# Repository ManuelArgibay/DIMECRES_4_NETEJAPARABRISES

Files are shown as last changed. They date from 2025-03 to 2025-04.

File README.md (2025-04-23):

# LIMPIA PARABRISAS

## Autores
- ManuelArgibay
- AlexY0916

## Versión - v1.01 Curso - Asignatura de Diseño de PCBs con KiCad - Curso 2024 - 2025

## Objectivo, Descripción breve del objectivo del proyecto.
Diseñar una placa PCB que desarrolle la función de limpiaparabrisas de un automóvil, mediante la detección de lluvia y accionamiento de motores, bombas de agua y un calefactor. Con el objetivo de mantener el parabrisas limpio y libre de objetos que puedan dificultar la visibilidad y evitar accidentes 

## Requisitos y especificaciones
- 2 motores con finales de carrera
- 2 bombas de líquido limpia parabrisas
- Sensor digital de lluvia
- Calefactor del vidrio

## Diagrama de bloques

## Tabla de componentes
| Descripción | Manufacturer Number | Package | Datasheet | Proveedor | Unidades |
| Microcontrolador | PIC18F258 | SOIC-28 | https://www.mouser.es/ProductDetail/Microchip-Technology/PIC18F258-I-SP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 | Mouser | 1 |
|Transceptor|MCP2551|SOIC-8|https://ww1.microchip.com/downloads/en/devicedoc/20001667g.pdf|Microchip|1|
|Amplificador operacional|LT1716|SOIC-5|https://www.mouser.es/datasheet/2/609/LT1716-1716222.pdf|Mouser|2|
|Regulador de tensión|LM117|TO-220|https://www.ti.com/lit/ds/symlink/lm1117.pdf?ts=1742942595976&ref_url=https%253A%252F%252Fbr.mouser.com%252F|Mouser|1|
|Puente H|DRV8871DDA|DDA|https://www.ti.com/lit/ds/symlink/drv8871-q1.pdf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||2|

## Funcionalidades
- Control de motores de limpiaparabrisas, bomba de agua y calefactor
- Detección de lluvia mediante sensor
- Botonera de acción manual

## Historial de cambios | Fecha | Autor | Branch | Descripción |
|1|25/03/2025|ManuelArgibay|main|Creación del proyecto|
|2|25/03/2025|ManuelArgibay|main|Cambio titulo del proyecto|
|3|25/03/2025|ManuelArgibay|main|Modificación del esquemático y pptx|
|4|25/03/2025|ManuelArgibay|main|Agrego net classes, proyecto y presentación |
|5|25/03/2025|AlexY0916|main|Modifico net classes, fc, GNDPWR, separación botonera|
|6|26/03/2025|AlexY0916|main|Separacion del circuito|
|7|29/03/2025|ManuelArgibay|main|Agrego presentaciones y archivos|
|8|29/03/2025|ManuelArgibay|main|Modifico simulaciones del comparador y arreglo esquematico|
|9|30/03/2025|AlexY0916|main|Ordenar esquematico|
|10|30/03/2025|AlexY0916|main|Footprint|
|11|30/03/2025|AlexY0916|main|Arreglar errores con los esquematicos|
|12|30/03/2025|AlexY0916|main|Empezando a añadir el sensor|
|13|31/03/2025|AlexY0916|main|Sensor|
|14|31/03/2025|AlexY0916|main|ICSP|
|15|31/03/2025|ManuelArgibay|main|Arreglo net classes y agrego DB-9|
|16|31/03/2025|ManuelArgibay|main|Empiezo layout, cambio footprints y arreglo esquematico|
|17|01/04/2025|ManuelArgibay|main|Termino layout|
|18|01/04/2025|ManuelArgibay|main|Arreglo nodos no conectados|
|19|01/04/2025|AlexY0916|main|Cambio el cristal|
|20|01/04/2025|AlexY0916|main|Cambio de presentacion, minimas correcciones en el esquematico|
|21|01/04/2025|AlexY0916|main|Nombrar etiqueta PCB|
|22|01/04/2025|AlexY0916|main|Cambio en la presentacion|
|23|02/04/2025|ManuelArgibay|main|Arreglo errores y cambio conector|
|24|02/04/2025|ManuelArgibay|main|Arreglo errores del DRC. Falta arreglar errores del GNDPWR|
|25|02/04/2025|ManuelArgibay|main|Preentrega final|
|26|02/04/2025|ManuelArgibay|main|Agrego cambios|
|27|07/04/2025|ManuelArgibay|main|Arreglo layout y esquematico con las correcciones pasadas|
|28|07/04/2025|AlexY0916|main|Separacion de la botonera|
|29|07/04/2025|AlexY0916|main|Cambio de valor los condensadores del oscilador|
|30|07/04/2025|AlexY0916|main|Cambio diagrama de bloques|
|31|08/04/2025|AlexY0916|main|Reglas de diseño|
|32|08/04/2025|AlexY0916|main|Cambiar esquematico|
|33|08/04/2025|AlexY0916|main|Cambio de la PCB (cambio de conectores)|
|34|09/04/2025|AlexY0916|main|Layout|
|35|09/04/2025|AlexY0916|main|Cambio del sensor|
|36|23/04/2025|ManuelArgibay|main|Arreglo layout y esquematico (DRC correcto)|

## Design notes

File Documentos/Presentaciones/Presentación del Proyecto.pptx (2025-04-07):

## Proyecto: Limpiaparabrisas

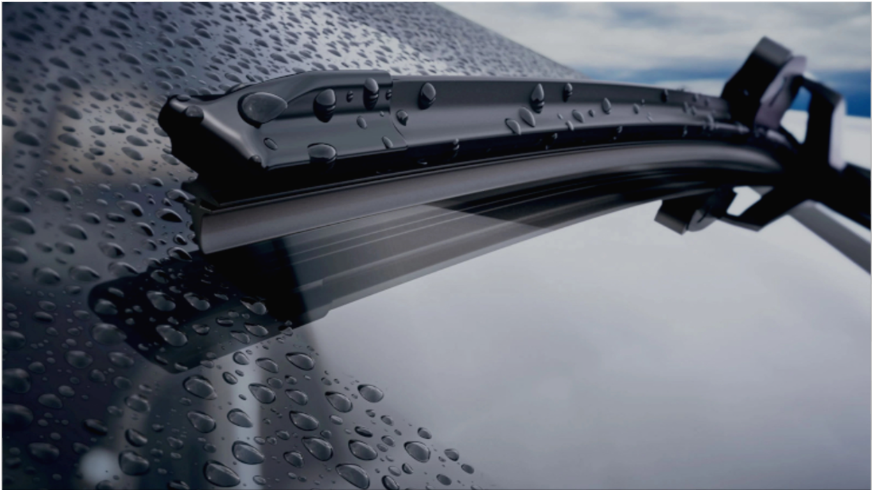
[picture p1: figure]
Les Escombretes Eixugaparabrises - Rodi Motor Services

Argibay Molina Manuel, Yang Alex

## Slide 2

Funcionalidad y objetivos

- Mantener el parabrisas limpio y libre de elementos que obstruyan la visión
  - Escobillas limpiaparabrisas controladas por motores.
  - Bombas de líquido limpia parabrisas.
  - Calefactor que evita el empañamiento del parabrisas.
  - Interfaz manual mediante botonera

- Diseñar e implementar este sistema en una PCB.
  - Garantizar funcionamiento y fiabilidad en el producto.
  - Optimización de energía.
  - Optimización de costos.

## Componentes

Microcontrolador PIC18FXX8
Transceptor MCP2551
Bus de programación y debug
Bus CAN
Bus I^2 C
Botonera

- Fuente de 12V
- Regulador de tensión
- 2 motores DC
- 2 bombas de líquido limpiaparabrisas
- Sensor digital de lluvia
- Calefactor del vidrio
- 2 puentes “H”
- 2 relés electromagnéticos
- 2 finales de carreras magnéticos

## Diagrama de Bloques

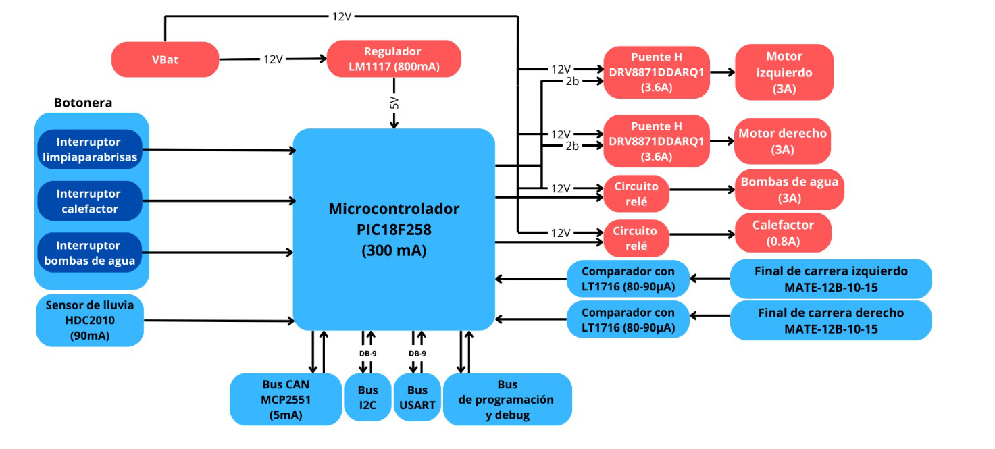
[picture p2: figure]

## Regulador de tensión

LM1117

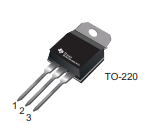
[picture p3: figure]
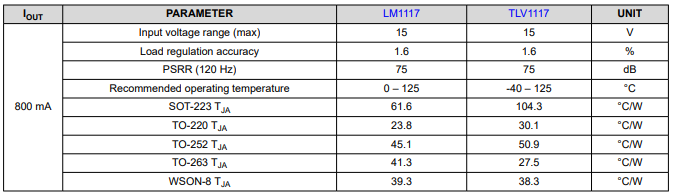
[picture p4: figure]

## Detector de lluvia

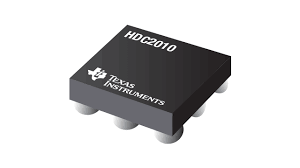
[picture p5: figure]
HDC2010 - Low Power Humidity and Temperature Sensor - Electronics-Lab.com

HDC2010

## Puente H

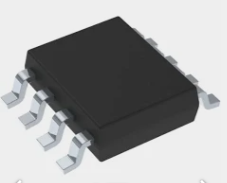
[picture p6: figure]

DRV8871DDARQ1

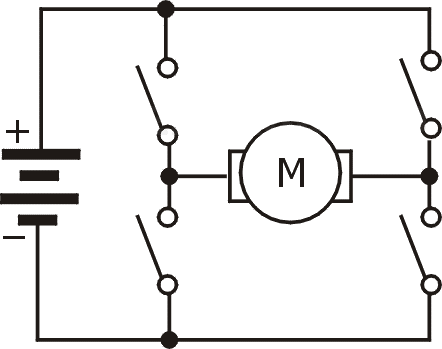
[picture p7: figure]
Control mediante puente en H | Control y robótica 4º E.S.O.

## Final de Carrera magnético (Reed Switch)

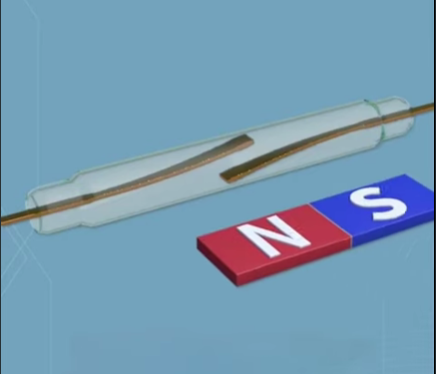
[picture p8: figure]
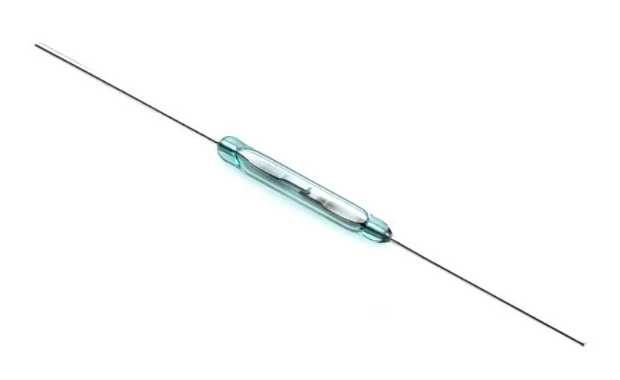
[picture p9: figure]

MATE-12B-10-15

## Amplificador Operacional

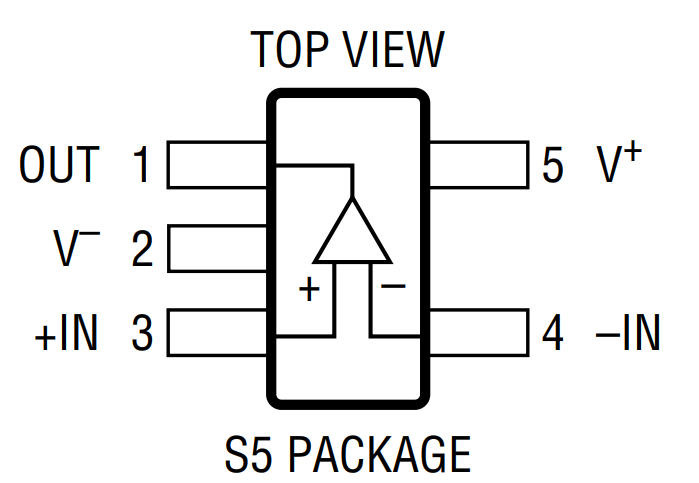
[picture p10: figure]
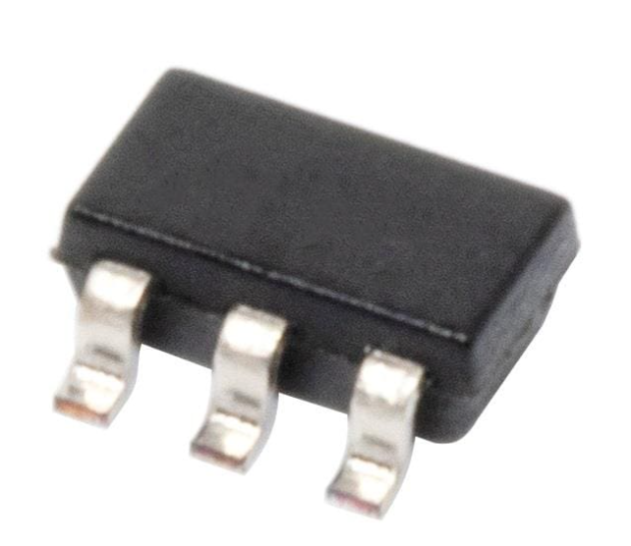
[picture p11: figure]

LT1716

## Esquemático del circuito

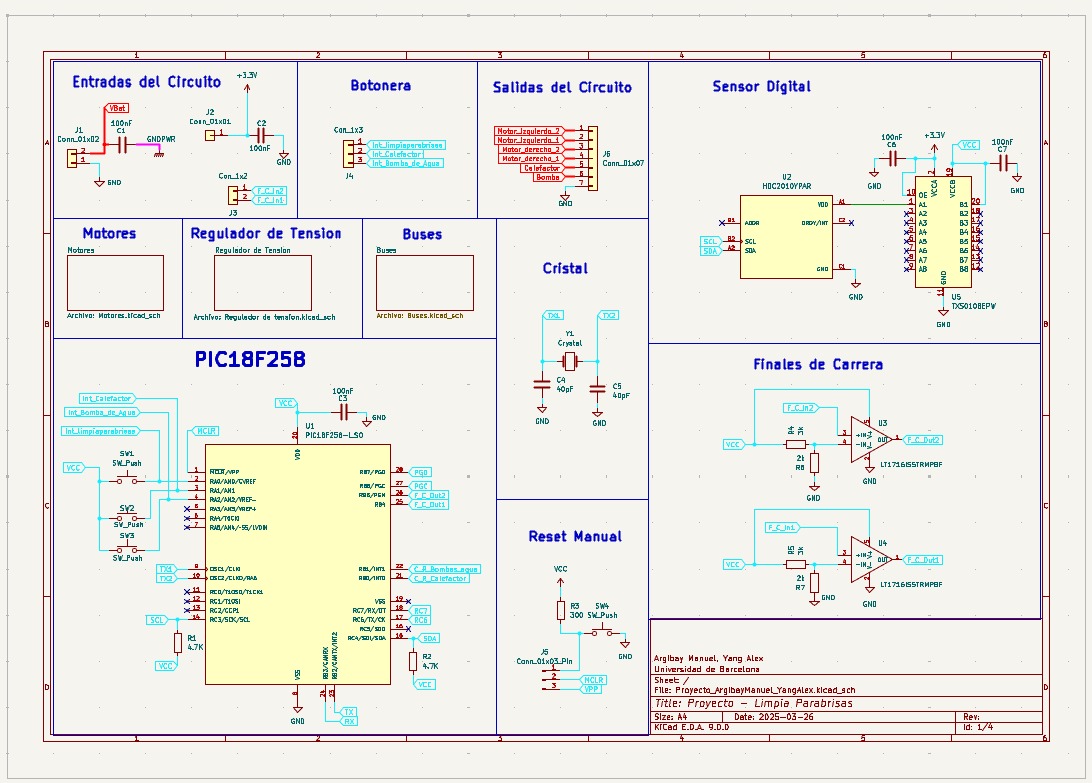
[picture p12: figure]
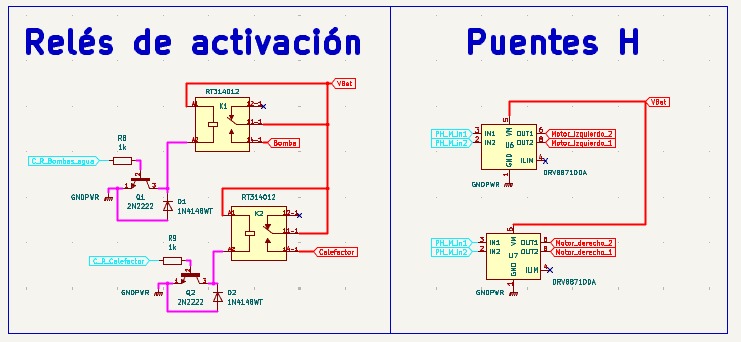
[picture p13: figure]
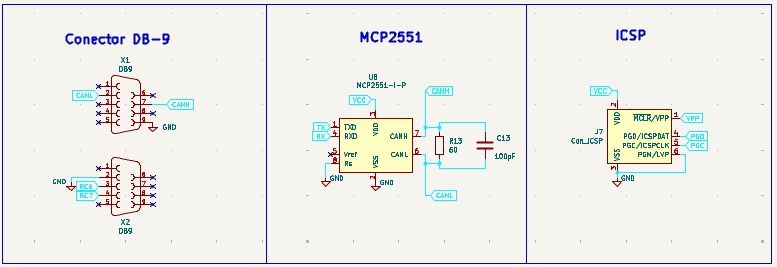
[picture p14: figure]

## Cambios

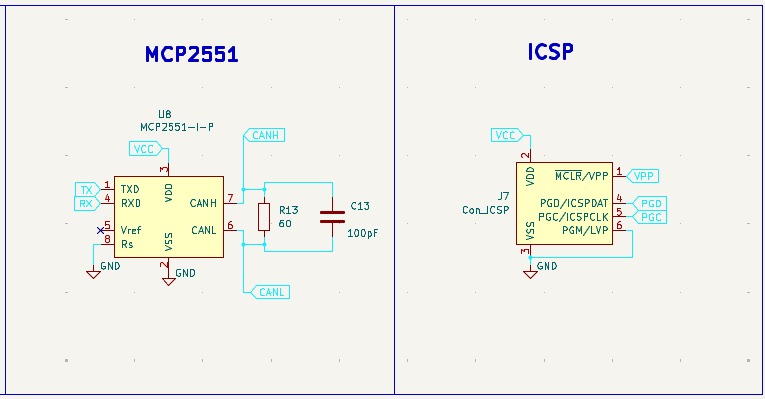
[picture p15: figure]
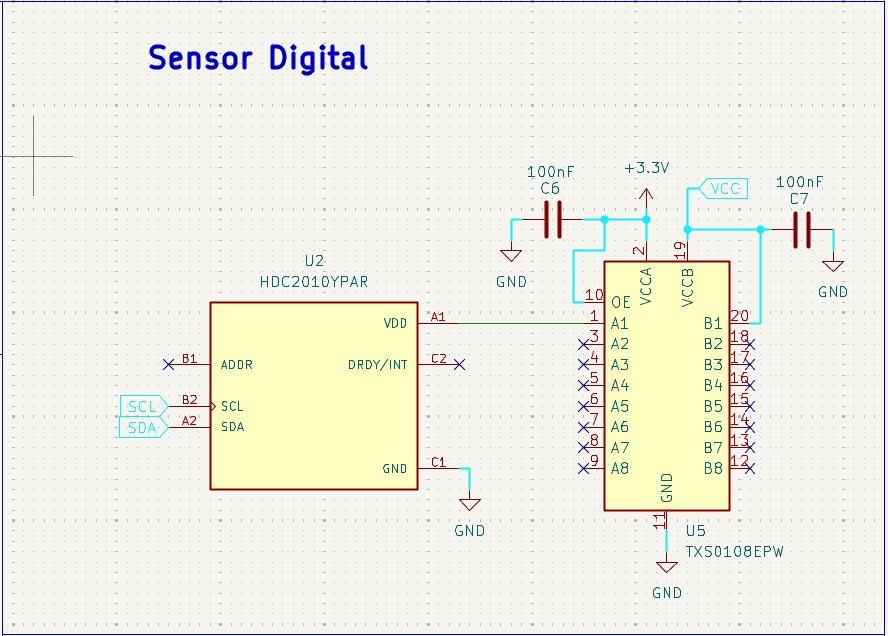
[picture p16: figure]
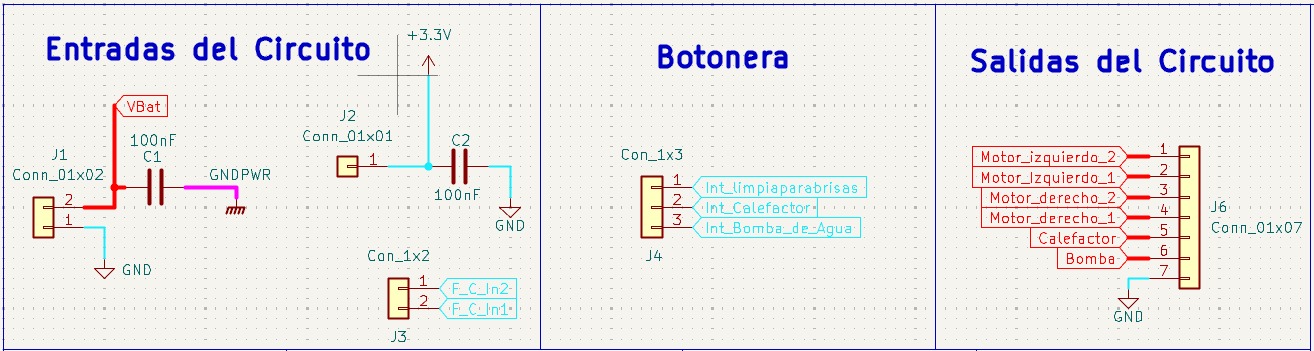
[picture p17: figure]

## Layout (TOP)

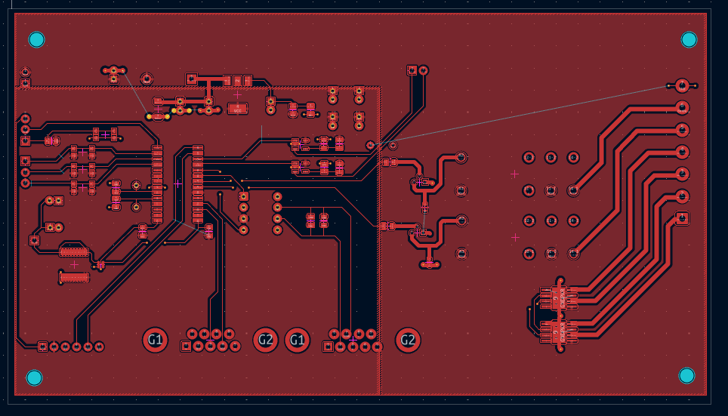
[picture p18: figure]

## Bottom

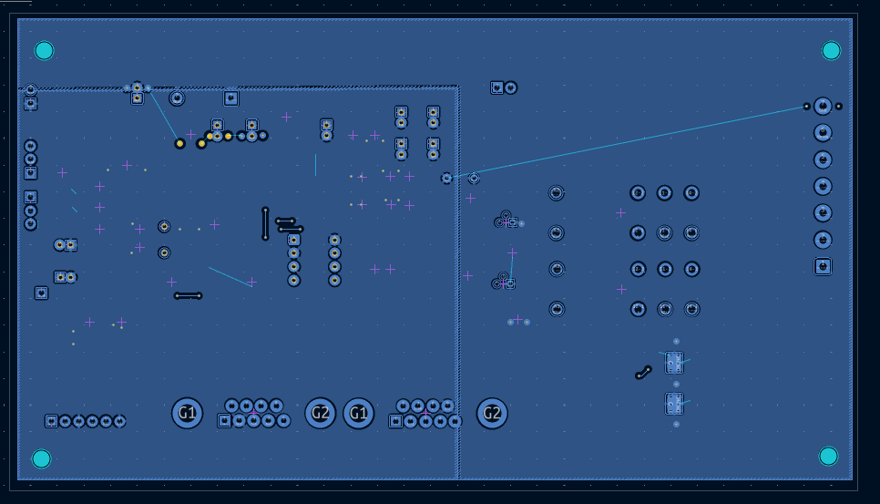
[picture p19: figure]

## Cosas a destacar del Layout

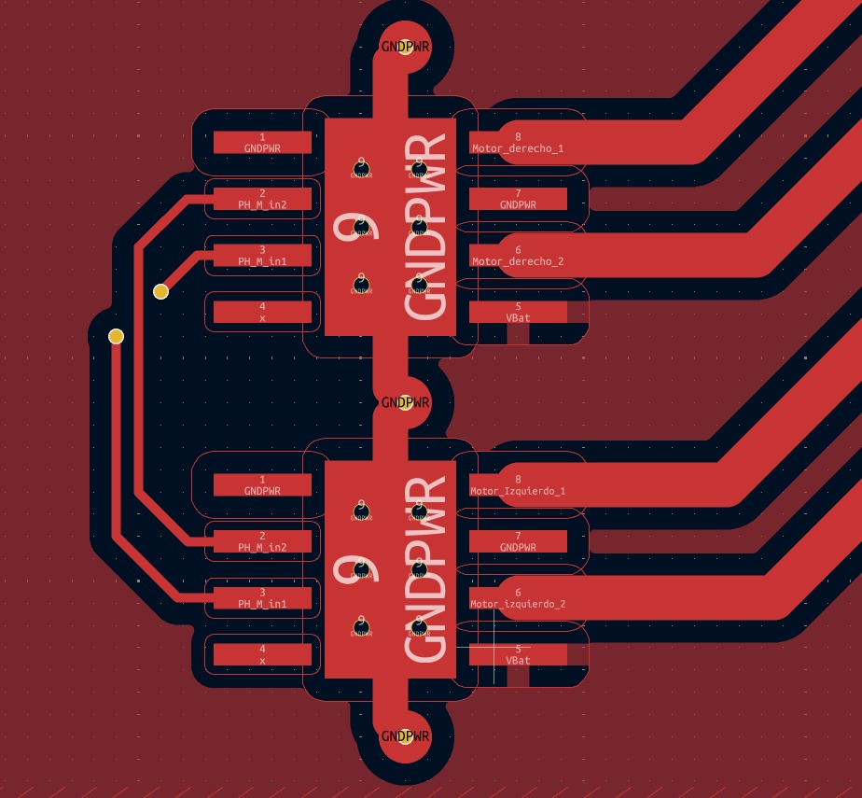
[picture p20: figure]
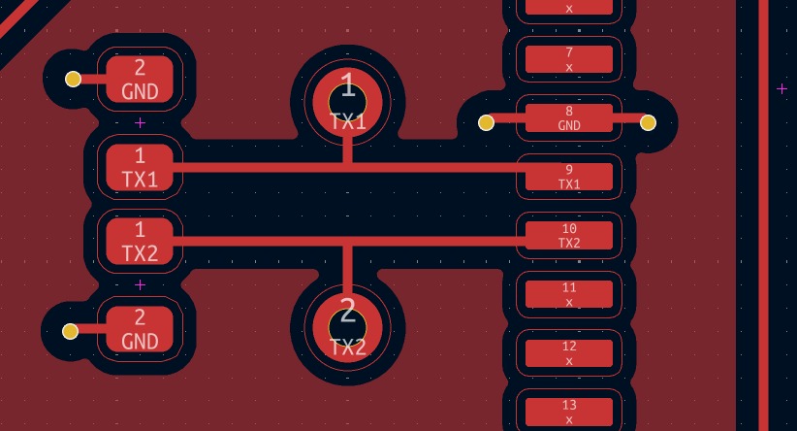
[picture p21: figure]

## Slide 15

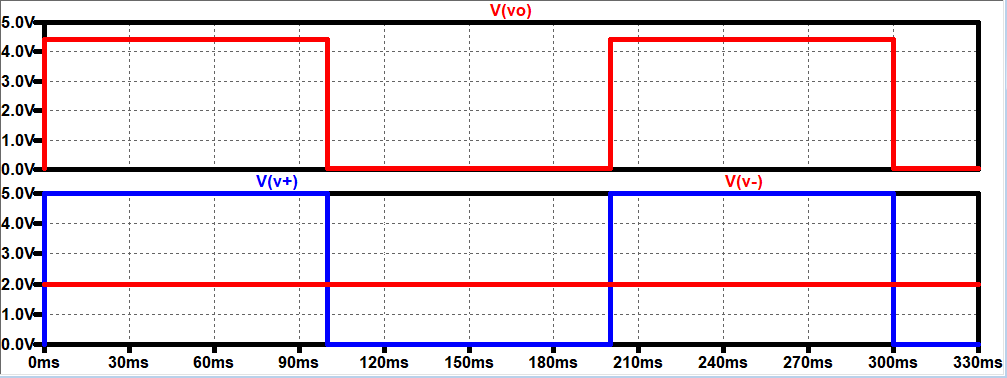
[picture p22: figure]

Simulación del comparador

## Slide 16

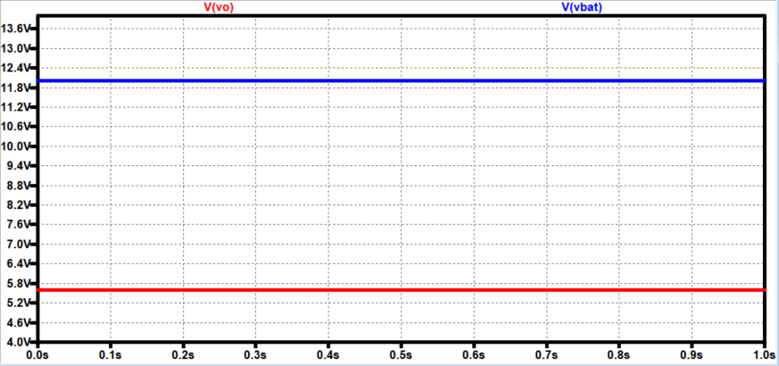
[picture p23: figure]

Simulación del
regulador

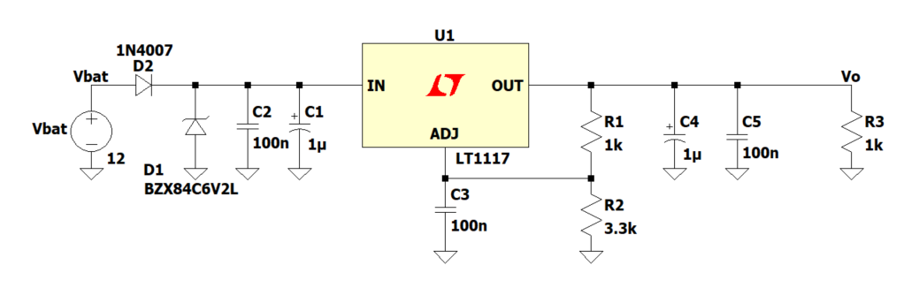
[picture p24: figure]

## Bibliografía

- Puente H: https://www.mouser.es/ProductDetail/Texas-Instruments/DRV8871DDARQ1?qs=AQlKX63v8RstMGgN6CYN5Q%3D%3D
- Final de carrera: https://www.mouser.es/ProductDetail/Littelfuse/MATE-12B-10-15?qs=VJzv269c%252BPbO1tueKz5qUA%3D%3D
- Sensor HIH6130: https://prod-edam.honeywell.com/content/dam/honeywell-edam/sps/siot/en-ca/products/sensors/humidity-with-temperature-sensors/honeywell-humidicon-hih6100-series/docum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
- Regulador LM1117: https://www.ti.com/lit/ds/symlink/lm1117.pdf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
- Calefactor: https://www.digikey.com/es/products/detail/riedon-products-by-bourns/PTCA-40/10271325
- Funcionamiento de Reed Switch: https://www.youtube.com/shorts/parNm9pB5Yw
- Opamp: https://www.mouser.es/ProductDetail/Analog-Devices/LT1716HS5WTRMPBF?qs=wnTfsH77Xs7Skv7hhFl%2Fog%3D%3D
- Relé: https://www.mouser.es/ProductDetail/Omron-Electronics/G5LE-1-DC12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
- BJT: https://www.mouser.es/ProductDetail/Central-Semiconductor/2N2222-PBFREE?qs=u16ybLDytRZWJogOmjHVFA%3D%3D

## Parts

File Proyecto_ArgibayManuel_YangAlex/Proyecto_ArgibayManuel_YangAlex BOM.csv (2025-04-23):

Reference | Qty | Value | DNP | Exclude from BOM | Exclude from Board | Footprint | Datasheet
C1,C2,C3,C6,C7,C8,C9,C10,C11,C13,C15 | 11 | 100nF |  |  |  | Capacitor_SMD:C_0805_2012Metric | ~
C4,C5 | 2 | 33pF |  |  |  | Capacitor_SMD:C_0805_2012Metric | ~
C12,C14 | 2 | 1uF |  |  |  | Capacitor_SMD:C_0805_2012Metric | ~
C16 | 1 | 100pF |  |  |  | Capacitor_SMD:C_0805_2012Metric | ~
D1,D2 | 2 | 1N4148WT |  |  |  | Diode_SMD:D_SOD-523 | https://www.diodes.com/assets/Datasheets/ds30396.pdf
D3 | 1 | 1N4002 |  |  |  | Diode_THT:D_DO-41_SOD81_P10.16mm_Horizontal | http://www.vishay.com/docs/88503/1n4001.pdf
D4 | 1 | BZV55C6V2 |  |  |  | Diode_SMD:D_MiniMELF | https://assets.nexperia.com/documents/data-sheet/BZV55_SER.pdf
IC1 | 1 | LM1117 |  |  |  | Footprints:LM1117
J1 | 1 | Conn_01x02 |  |  |  | Connector_PinHeader_2.54mm:PinHeader_1x02_P2.54mm_Vertical | ~
J2 | 1 | Conn_01x01 |  |  |  | Connector_PinHeader_2.54mm:PinHeader_1x01_P2.54mm_Vertical | ~
J3,J4,J5,J6 | 4 | Con_1x2 |  |  |  | Connector_PinHeader_2.54mm:PinHeader_1x02_P2.54mm_Vertical | ~
J7,J8 | 2 | Conn_01x03 |  |  |  | TerminalBlock_Phoenix:TerminalBlock_Phoenix_MKDS-3-3-5.08_1x03_P5.08mm_Horizontal | ~
J9 | 1 | Conn_01x03_Pin |  |  |  | Connector_PinHeader_2.54mm:PinHeader_1x03_P2.54mm_Vertical | ~
J10,J11 | 2 | Con_1x2 |  |  |  | TerminalBlock_Phoenix:TerminalBlock_Phoenix_MKDS-3-2-5.08_1x02_P5.08mm_Horizontal | ~
J12 | 1 | Con_ICSP |  |  |  | Connector_PinHeader_2.54mm:PinHeader_1x06_P2.54mm_Vertical | http://ww1.microchip.com/downloads/en/devicedoc/30277d.pdf
K1,K2 | 2 | RT314012 |  |  |  | Footprints:RT314012
Q1,Q2 | 2 | 2N2222 |  |  |  | Footprints:2N2222
R1,R2,R8,R9 | 4 | 4.7K |  |  |  | Resistor_SMD:R_0805_2012Metric | ~
R3 | 1 | 300 |  |  |  | Resistor_SMD:R_0805_2012Metric | ~
R4,R5 | 2 | 3k |  |  |  | Resistor_SMD:R_0805_2012Metric | ~
R6,R7 | 2 | 2k |  |  |  | Resistor_SMD:R_0805_2012Metric | ~
R10,R11,R12,R13,R15,R16 | 6 | 1k |  |  |  | Resistor_SMD:R_0805_2012Metric | ~
R14 | 1 | 0 |  |  |  | Resistor_THT:R_Axial_DIN0204_L3.6mm_D1.6mm_P5.08mm_Vertical | ~
R17 | 1 | 60 |  |  |  | Resistor_SMD:R_0805_2012Metric | ~
SW1,SW2,SW3,SW4 | 4 | SW_Push |  |  |  | Button_Switch_SMD:SW_Push_1P1T_NO_CK_KMR2 | ~
U1 | 1 | PIC18F258-I_SO |  |  |  | Footprints:PIC18F258
U2 | 1 | HDC2010YPAR |  |  |  | Footprints:HDC2010YPAR
U3,U4 | 2 | LT1716IS5TRMPBF |  |  |  | Footprints:LT1716
U5 | 1 | TXS0108EPW |  |  |  | Package_SO:TSSOP-20_4.4x6.5mm_P0.65mm | www.ti.com/lit/ds/symlink/txs0108e.pdf
U6,U7 | 2 | DRV8871DDA |  |  |  | Package_SO:Texas_HTSOP-8-1EP_3.9x4.9mm_P1.27mm_EP2.95x4.9mm_Mask2.4x3.1mm_ThermalVias | http://www.ti.com/lit/ds/symlink/drv8871.pdf
U8 | 1 | MCP2551-I-P |  |  |  | Package_DIP:DIP-8_W7.62mm | http://ww1.microchip.com/downloads/en/devicedoc/21667d.pdf
X1,X2 | 2 | DB9 |  |  |  | Footprints:DB9
Y1 | 1 | Crystal |  |  |  | Crystal:Crystal_HC49-U_Vertical | ~

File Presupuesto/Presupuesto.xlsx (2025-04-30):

x10 |  |  |  |  |  |  | x50
Producto | Descripción | Enlace | Cantidad por PCB | Cantidad total | Precio por unidad | Total | Producto | Descripción | Enlace | Cantidad por PCB | Cantidad total | Precio por unidad | Total
Resistencia 4.7KΩ | ERA-6VEB4701V | https://www.mouser.es/ProductDetail/Panasonic/ERA-6VEB4701V | 4 | 40 | 0.24 € | 9.60 € | Resistencia 4.7KΩ | ERA-6VEB4701V | https://www.mouser.es/ProductDetail/Panasonic/ERA-6VEB4701V | 4 | 200 | 0.21 € | 42.00 €
Resistencia 3KΩ | TNPW08053K00FEEA | https://www.mouser.es/ProductDetail/Vishay-Dale/TNPW08053K00FEEA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 | 2 | 20 | 0.12 € | 2.48 € | Resistencia 3KΩ | TNPW08053K00FEEA | https://www.mouser.es/ProductDetail/Vishay-Dale/TNPW08053K00FEEA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 | 2 | 100 | 0.10 € | 10.30 €
Resistencia 2KΩ | ERJ-UP6D2001V | https://www.mouser.es/ProductDetail/Panasonic/ERJ-UP6D2001V | 2 | 20 | 0.14 € | 2.72 € | Resistencia 2KΩ | ERJ-UP6D2001V | https://www.mouser.es/ProductDetail/Panasonic/ERJ-UP6D2001V | 2 | 100 | 0.08 € | 7.90 €
Resistencia 1KΩ | ERA-6AED102V | https://www.mouser.es/ProductDetail/Panasonic/ERA-6AED102V | 6 | 60 | 0.18 € | 10.68 € | Resistencia 1KΩ | ERA-6AED102V | https://www.mouser.es/ProductDetail/Panasonic/ERA-6AED102V | 6 | 300 | 0.10 € | 31.50 €
Resistencia 300Ω | SFR10EZPF3000 | https://www.mouser.es/ProductDetail/ROHM-Semiconductor/SFR10EZPF3000 | 1 | 10 | 0.09 € | 0.89 € | Resistencia 300Ω | SFR10EZPF3000 | https://www.mouser.es/ProductDetail/ROHM-Semiconductor/SFR10EZPF3000 | 1 | 50 | 0.09 € | 4.45 €
Resistencia 68Ω | MCU08050C6809FP500 | https://www.mouser.es/ProductDetail/Vishay-Beyschlag/MCU08050C6809FP500 | 1 | 10 | 0.16 € | 1.62 € | Resistencia 68Ω | MCU08050C6809FP500 | https://www.mouser.es/ProductDetail/Vishay-Beyschlag/MCU08050C6809FP500 | 1 | 50 | 0.16 € | 8.10 €
Capacitor 1uF | KGM21AR71C105JU | https://www.mouser.es/ProductDetail/KYOCERA-AVX/KGM21AR71C105JU?qs=Jm2GQyTW%2FbgRn%252Bi87%2FZsQQ%3D%3D | 2 | 20 | 0.16 € | 3.14 € | Capacitor 1uF | KGM21AR71C105JU | https://www.mouser.es/ProductDetail/KYOCERA-AVX/KGM21AR71C105JU?qs=Jm2GQyTW%2FbgRn%252Bi87%2FZsQQ%3D%3D | 2 | 100 | 0.09 € | 9.30 €
Capacitor 100nF | VJ0805Y104KXBAT | https://www.mouser.es/ProductDetail/Vishay-Vitramon/VJ0805Y104KXBAT?qs=ZB8tH5z5N7bogYVWlZJLKw%3D%3D | 11 | 110 | 0.22 € | 24.20 € | Capacitor 100nF | VJ0805Y104KXBAT | https://www.mouser.es/ProductDetail/Vishay-Vitramon/VJ0805Y104KXBAT?qs=ZB8tH5z5N7bogYVWlZJLKw%3D%3D | 11 | 550 | 0.18 € | 99.00 €
Capacitor 100pF | 08051C101JAT2A | https://www.mouser.es/ProductDetail/KYOCERA-AVX/08051C101JAT2A?qs=LzfKPbejVBU01Un%2F7H3NFQ%3D%3D | 1 | 10 | 0.11 € | 1.14 € | Capacitor 100pF | 08051C101JAT2A | https://www.mouser.es/ProductDetail/KYOCERA-AVX/08051C101JAT2A?qs=LzfKPbejVBU01Un%2F7H3NFQ%3D%3D | 1 | 50 | 0.11 € | 5.70 €
Capacitor 33pF | 08052U330JAT2A | https://www.mouser.es/ProductDetail/KYOCERA-AVX/08052U330JAT2A?qs=PWqgEMkqndQIleO2EF3Tsw%3D%3D | 2 | 20 | 0.19 € | 3.84 € | Capacitor 33pF | 08052U330JAT2A | https://www.mouser.es/ProductDetail/KYOCERA-AVX/08052U330JAT2A?qs=PWqgEMkqndQIleO2EF3Tsw%3D%3D | 2 | 100 | 0.11 € | 10.90 €
Diodo 1N4148 | 1N4148WT-7 | https://www.mouser.es/ProductDetail/Diodes-Incorporated/1N4148WT-7?qs=FITO%2F%2FQgYDlMYETivVNccQ%3D%3D | 2 | 20 | 0.06 € | 1.14 € | Diodo 1N4148 | 1N4148WT-7 | https://www.mouser.es/ProductDetail/Diodes-Incorporated/1N4148WT-7?qs=FITO%2F%2FQgYDlMYETivVNccQ%3D%3D | 2 | 100 | 0.05 € | 5.30 €
Diodo 1N4002 | 1N4002-T | https://www.mouser.es/ProductDetail/Diodes-Incorporated/1N4002-T?qs=rGAXPo9uwV21tVJRR%252BhxrQ%3D%3D | 1 | 10 | 0.12 € | 1.19 € | Diodo 1N4002 | 1N4002-T | https://www.mouser.es/ProductDetail/Diodes-Incorporated/1N4002-T?qs=rGAXPo9uwV21tVJRR%252BhxrQ%3D%3D | 1 | 50 | 0.12 € | 5.95 €
Diodo BZV55C6V2 | BZV55C6V2 | https://www.mouser.es/ProductDetail/Taiwan-Semiconductor/BZV55C6V2?qs=tHU%2FlV7kTyT6aGdLZjLeJA%3D%3D | 1 | 10 | 0.13 € | 1.32 € | Diodo BZV55C6V2 | BZV55C6V2 | https://www.mouser.es/ProductDetail/Taiwan-Semiconductor/BZV55C6V2?qs=tHU%2FlV7kTyT6aGdLZjLeJA%3D%3D | 1 | 50 | 0.13 € | 6.60 €
Regulador de tensión | LM1117T | https://www.mouser.es/ProductDetail/Texas-Instruments/LM1117T-3.3-NOPB?qs=X1J7HmVL2ZF7RIQB6O0mNg%3D%3D | 1 | 10 | 1.10 € | 11.00 € | Regulador de tensión | LM1117T | https://www.mouser.es/ProductDetail/Texas-Instruments/LM1117T-3.3-NOPB?qs=X1J7HmVL2ZF7RIQB6O0mNg%3D%3D | 1 | 50 | 0.95 € | 47.45 €
Conector 1x1 | PH1-01-UA | https://www.digikey.com/en/products/detail/adam-tech/PH1-01-UA/9830231 | 1 | 10 | 0.02 € | 0.18 € | Conector 1x1 | PH1-01-UA | https://www.digikey.com/en/products/detail/adam-tech/PH1-01-UA/9830231 | 1 | 50 | 0.02 € | 0.90 €
Conector 1x2 | 61300211121 | https://www.digikey.com/en/products/detail/w%C3%BCrth-elektronik/61300211121/4846823 | 5 | 50 | 0.08 € | 4.00 € | Conector 1x2 | 61300211121 | https://www.digikey.com/en/products/detail/w%C3%BCrth-elektronik/61300211121/4846823 | 5 | 250 | 0.06 € | 15.97 €
Conector 1x3 | M20-9990345 | https://www.digikey.com/en/products/detail/harwin-inc/M20-9990345/3728227 | 1 | 10 | 0.12 € | 1.23 € | Conector 1x3 | M20-9990345 | https://www.digikey.com/en/products/detail/harwin-inc/M20-9990345/3728227 | 1 | 50 | 0.12 € | 6.20 €
Conector 1x6 | 61300611121 | https://www.digikey.com/en/products/detail/w%C3%BCrth-elektronik/61300611121/4846833 | 1 | 10 | 0.27 € | 2.68 € | Conector 1x6 | 61300611121 | https://www.digikey.com/en/products/detail/w%C3%BCrth-elektronik/61300611121/4846833 | 1 | 50 | 0.19 € | 9.30 €
Conector BLK 1x2 | 1729128 | https://www.digikey.com/en/products/detail/phoenix-contact/1729128/260615 | 2 | 20 | 0.95 € | 19.00 € | Conector BLK 1x2 | 1729128 | https://www.digikey.com/en/products/detail/phoenix-contact/1729128/260615 | 2 | 100 | 0.84 € | 84.00 €
Conector BLK 1x3 | 1729131 | https://www.digikey.com/en/products/detail/phoenix-contact/1729131/260616 | 2 | 20 | 1.38 € | 27.58 € | Conector BLK 1x3 | 1729131 | https://www.digikey.com/en/products/detail/phoenix-contact/1729131/260616 | 2 | 100 | 1.27 € | 127.10 €
Relé | RT314012 | https://www.mouser.es/ProductDetail/TE-Connectivity-PB/RT314012?qs=h4sDRd%2FXttjfRhAgOQMm4w%3D%3D | 2 | 20 | 2.67 € | 53.40 € | Relé | RT314012 | https://www.mouser.es/ProductDetail/TE-Connectivity-PB/RT314012?qs=h4sDRd%2FXttjfRhAgOQMm4w%3D%3D | 2 | 100 | 2.60 € | 260.00 €
Transistor BJT | 2N2222 | https://www.digikey.es/es/products/detail/central-semiconductor-corp/2N2222-PBFREE/4806844?gQT=2 | 2 | 20 | 1.90 € | 38.08 € | Transistor BJT | 2N2222 | https://www.digikey.es/es/products/detail/central-semiconductor-corp/2N2222-PBFREE/4806844?gQT=2 | 2 | 100 | 1.32 € | 132.00 €
Botón | PTS526SK15SMTR2-LFS | https://www.digikey.es/es/products/detail/c-k/PTS526SK15SMTR2-LFS/10056626 | 4 | 40 | 0.12 € | 4.76 € | Botón | PTS526SK15SMTR2-LFS | https://www.digikey.es/es/products/detail/c-k/PTS526SK15SMTR2-LFS/10056626 | 4 | 200 | 0.11 € | 21.40 €
Microcontrolador | PIC18F2580-I/SO | https://www.mouser.es/ProductDetail/Microchip-Technology/PIC18F2580-I-SO?qs=5Wx0vN22rFLg5k%2FqM4Xm9A%3D%3D | 1 | 10 | 7.72 € | 77.20 € | Microcontrolador | PIC18F2580-I/SO | https://www.mouser.es/ProductDetail/Microchip-Technology/PIC18F2580-I-SO?qs=5Wx0vN22rFLg5k%2FqM4Xm9A%3D%3D | 1 | 50 | 7.72 € | 386.00 €
Sensor de lluvia | HDC2010YPAR | https://www.mouser.es/ProductDetail/Texas-Instruments/HDC2010YPAR?qs=EU6FO9ffTwc2CasHMLP4bA%3D%3D | 1 | 10 | 1.23 € | 12.30 € | Sensor de lluvia | HDC2010YPAR | https://www.mouser.es/ProductDetail/Texas-Instruments/HDC2010YPAR?qs=EU6FO9ffTwc2CasHMLP4bA%3D%3D | 1 | 50 | 1.18 € | 59.00 €
Amplificador Operacional | LT1716 | https://www.mouser.es/ProductDetail/Analog-Devices/LT1716IS5TRMPBF?qs=ytflclh7QUVIaNMG%252B3EIxQ%3D%3D | 2 | 20 | 2.98 € | 59.60 € | Amplificador Operacional | LT1716 | https://www.mouser.es/ProductDetail/Analog-Devices/LT1716IS5TRMPBF?qs=ytflclh7QUVIaNMG%252B3EIxQ%3D%3D | 2 | 100 | 2.46 € | 246.00 €
Transceptor de Voltaje | TXS0108EPWR | https://www.mouser.es/ProductDetail/Texas-Instruments/TXS0108EPWR?qs=IUbkBnfnSQLgiWtCbWtYOw%3D%3D | 1 | 10 | 0.86 € | 8.60 € | Transceptor de Voltaje | TXS0108EPWR | https://www.mouser.es/ProductDetail/Texas-Instruments/TXS0108EPWR?qs=IUbkBnfnSQLgiWtCbWtYOw%3D%3D | 1 | 50 | 0.78 € | 38.95 €
Puente H | DRV8871DDA | https://www.digikey.com/es/products/detail/texas-instruments/DRV8871DDA/6110574 | 2 | 20 | 2.40 € | 48.08 € | Puente H | DRV8871DDA | https://www.digikey.com/es/products/detail/texas-instruments/DRV8871DDA/6110574 | 2 | 100 | 2.02 € | 202.00 €
Controlador CAN | MCP2551 | https://www.mouser.es/ProductDetail/Microchip-Technology/MCP2551-E-SN?qs=Vn0zuzr35GHkGDCgnw0F9A%3D%3D | 1 | 10 | 1.51 € | 15.10 € | Controlador CAN | MCP2551 | https://www.mouser.es/ProductDetail/Microchip-Technology/MCP2551-E-SN?qs=Vn0zuzr35GHkGDCgnw0F9A%3D%3D | 1 | 50 | 1.48 € | 74.00 €
Conector DB9 | SD9S | https://www.digikey.es/es/products/detail/l-com/SD9S/21288632 | 2 | 20 | 3.47 € | 69.36 € | Conector DB9 | SD9S | https://www.digikey.es/es/products/detail/l-com/SD9S/21288632 | 2 | 100 | 2.94 € | 294.00 €
Cristal | HC-49/U | https://www.digikey.es/es/products/detail/citizen-finedevice-co-ltd/HC-49-U-S16384000ABJB/284225 | 1 | 10 | 0.43 € | 4.28 € | Cristal | HC-49/U | https://www.digikey.es/es/products/detail/citizen-finedevice-co-ltd/HC-49-U-S16384000ABJB/284225 | 1 | 50 | 0.39 € | 19.40 €
PCB | - | https://cart.jlcpcb.com/quote?orderType=1&stencilLayer=1&stencilWidth=100&stencilLength=100&stencilCounts=2000 | 1 | 10 | 1.79 € | 17.90 € | PCB | - | https://cart.jlcpcb.com/quote?orderType=1&stencilLayer=1&stencilWidth=100&stencilLength=100&stencilCounts=2000 | 1 | 50 | 1.07 € | 53.40 €
 |  |  |  |  | Total: | 538.29 € |  |  |  |  |  | Total: | 2324.07 €
 |  |  |  |  | Total por placa: | 53.83 € |  |  |  |  |  | Total por placa: | 46.48 €
x1000 |  |  |  |  |  |  | x20000
Producto | Descripción | Enlace | Cantidad por PCB | Cantidad total | Precio por unidad | Total | Producto | Descripción | Enlace | Cantidad por PCB | Cantidad total | Precio por unidad | Total
Resistencia 4.7KΩ | ERA-6VEB4701V | https://www.mouser.es/ProductDetail/Panasonic/ERA-6VEB4701V | 4 | 4000 | 0.20 € | 784.00 € | Resistencia 4.7KΩ | ERA-6VEB4701V | https://www.mouser.es/ProductDetail/Panasonic/ERA-6VEB4701V | 4 | 80000 | 0.17 € | 13600.00 €
Resistencia 3KΩ | TNPW08053K00FEEA | https://www.mouser.es/ProductDetail/Vishay-Dale/TNPW08053K00FEEA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 | 2 | 2000 | 0.08 € | 168.00 € | Resistencia 3KΩ | TNPW08053K00FEEA | https://www.mouser.es/ProductDetail/Vishay-Dale/TNPW08053K00FEEA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 | 2 | 40000 | 0.06 € | 2480.00 €
Resistencia 2KΩ | ERJ-UP6D2001V | https://www.mouser.es/ProductDetail/Panasonic/ERJ-UP6D2001V | 2 | 2000 | 0.05 € | 102.00 € | Resistencia 2KΩ | ERJ-UP6D2001V | https://www.mouser.es/ProductDetail/Panasonic/ERJ-UP6D2001V | 2 | 40000 | 0.04 € | 1560.00 €
Resistencia 1KΩ | ERA-6AED102V | https://www.mouser.es/ProductDetail/Panasonic/ERA-6AED102V | 6 | 6000 | 0.06 € | 336.00 € | Resistencia 1KΩ | ERA-6AED102V | https://www.mouser.es/ProductDetail/Panasonic/ERA-6AED102V | 6 | 120000 | 0.05 € | 6120.00 €
Resistencia 300Ω | SFR10EZPF3000 | https://www.mouser.es/ProductDetail/ROHM-Semiconductor/SFR10EZPF3000 | 1 | 1000 | 0.03 € | 31.00 € | Resistencia 300Ω | SFR10EZPF3000 | https://www.mouser.es/ProductDetail/ROHM-Semiconductor/SFR10EZPF3000 | 1 | 20000 | 0.02 € | 440.00 €
Resistencia 68Ω | MCU08050C6809FP500 | https://www.mouser.es/ProductDetail/Vishay-Beyschlag/MCU08050C6809FP500 | 1 | 1000 | 0.06 € | 64.00 € | Resistencia 68Ω | MCU08050C6809FP500 | https://www.mouser.es/ProductDetail/Vishay-Beyschlag/MCU08050C6809FP500 | 1 | 20000 | 0.06 € | 1280.00 €
Capacitor 1uF | KGM21AR71C105JU | https://www.mouser.es/ProductDetail/KYOCERA-AVX/KGM21AR71C105JU?qs=Jm2GQyTW%2FbgRn%252Bi87%2FZsQQ%3D%3D | 2 | 2000 | 0.07 € | 134.00 € | Capacitor 1uF | KGM21AR71C105JU | https://www.mouser.es/ProductDetail/KYOCERA-AVX/KGM21AR71C105JU?qs=Jm2GQyTW%2FbgRn%252Bi87%2FZsQQ%3D%3D | 2 | 40000 | 0.05 € | 1960.00 €
Capacitor 100nF | VJ0805Y104KXBAT | https://www.mouser.es/ProductDetail/Vishay-Vitramon/VJ0805Y104KXBAT?qs=ZB8tH5z5N7bogYVWlZJLKw%3D%3D | 11 | 11000 | 0.13 € | 1430.00 € | Capacitor 100nF | VJ0805Y104KXBAT | https://www.mouser.es/ProductDetail/Vishay-Vitramon/VJ0805Y104KXBAT?qs=ZB8tH5z5N7bogYVWlZJLKw%3D%3D | 11 | 220000 | 0.12 € | 26400.00 €
Capacitor 100pF | 08051C101JAT2A | https://www.mouser.es/ProductDetail/KYOCERA-AVX/08051C101JAT2A?qs=LzfKPbejVBU01Un%2F7H3NFQ%3D%3D | 1 | 1000 | 0.05 € | 46.00 € | Capacitor 100pF | 08051C101JAT2A | https://www.mouser.es/ProductDetail/KYOCERA-AVX/08051C101JAT2A?qs=LzfKPbejVBU01Un%2F7H3NFQ%3D%3D | 1 | 20000 | 0.04 € | 760.00 €
Capacitor 33pF | 08052U330JAT2A | https://www.mouser.es/ProductDetail/KYOCERA-AVX/08052U330JAT2A?qs=PWqgEMkqndQIleO2EF3Tsw%3D%3D | 2 | 2000 | 0.09 € | 178.00 € | Capacitor 33pF | 08052U330JAT2A | https://www.mouser.es/ProductDetail/KYOCERA-AVX/08052U330JAT2A?qs=PWqgEMkqndQIleO2EF3Tsw%3D%3D | 2 | 40000 | 0.05 € | 2120.00 €
Diodo 1N4148 | 1N4148WT-7 | https://www.mouser.es/ProductDetail/Diodes-Incorporated/1N4148WT-7?qs=FITO%2F%2FQgYDlMYETivVNccQ%3D%3D | 2 | 2000 | 0.04 € | 78.00 € | Diodo 1N4148 | 1N4148WT-7 | https://www.mouser.es/ProductDetail/Diodes-Incorporated/1N4148WT-7?qs=FITO%2F%2FQgYDlMYETivVNccQ%3D%3D | 2 | 40000 | 0.02 € | 880.00 €
Diodo 1N4002 | 1N4002-T | https://www.mouser.es/ProductDetail/Diodes-Incorporated/1N4002-T?qs=rGAXPo9uwV21tVJRR%252BhxrQ%3D%3D | 1 | 1000 | 0.03 € | 34.00 € | Diodo 1N4002 | 1N4002-T | https://www.mouser.es/ProductDetail/Diodes-Incorporated/1N4002-T?qs=rGAXPo9uwV21tVJRR%252BhxrQ%3D%3D | 1 | 20000 | 0.03 € | 560.00 €
Diodo BZV55C6V2 | BZV55C6V2 | https://www.mouser.es/ProductDetail/Taiwan-Semiconductor/BZV55C6V2?qs=tHU%2FlV7kTyT6aGdLZjLeJA%3D%3D | 1 | 1000 | 0.04 € | 39.00 € | Diodo BZV55C6V2 | BZV55C6V2 | https://www.mouser.es/ProductDetail/Taiwan-Semiconductor/BZV55C6V2?qs=tHU%2FlV7kTyT6aGdLZjLeJA%3D%3D | 1 | 20000 | 0.03 € | 520.00 €
Regulador de tensión | LM1117T | https://www.mouser.es/ProductDetail/Texas-Instruments/LM1117T-3.3-NOPB?qs=X1J7HmVL2ZF7RIQB6O0mNg%3D%3D | 1 | 1000 | 0.80 € | 801.00 € | Regulador de tensión | LM1117T | https://www.mouser.es/ProductDetail/Texas-Instruments/LM1117T-3.3-NOPB?qs=X1J7HmVL2ZF7RIQB6O0mNg%3D%3D | 1 | 20000 | 0.73 € | 14660.00 €
Conector 1x1 | PH1-01-UA | https://www.digikey.com/en/products/detail/adam-tech/PH1-01-UA/9830231 | 1 | 1000 | 0.01 € | 12.60 € | Conector 1x1 | PH1-01-UA | https://www.digikey.com/en/products/detail/adam-tech/PH1-01-UA/9830231 | 1 | 20000 | 0.01 € | 214.00 €
Conector 1x2 | 61300211121 | https://www.digikey.com/en/products/detail/w%C3%BCrth-elektronik/61300211121/4846823 | 5 | 5000 | 0.06 € | 300.00 € | Conector 1x2 | 61300211121 | https://www.digikey.com/en/products/detail/w%C3%BCrth-elektronik/61300211121/4846823 | 5 | 100000 | 0.06 € | 6000.00 €
Conector 1x3 | M20-9990345 | https://www.digikey.com/en/products/detail/harwin-inc/M20-9990345/3728227 | 1 | 1000 | 0.09 € | 89.00 € | Conector 1x3 | M20-9990345 | https://www.digikey.com/en/products/detail/harwin-inc/M20-9990345/3728227 | 1 | 20000 | 0.08 € | 1521.20 €
Conector 1x6 | 61300611121 | https://www.digikey.com/en/products/detail/w%C3%BCrth-elektronik/61300611121/4846833 | 1 | 1000 | 0.15 € | 153.00 € | Conector 1x6 | 61300611121 | https://www.digikey.com/en/products/detail/w%C3%BCrth-elektronik/61300611121/4846833 | 1 | 20000 | 0.15 € | 3078.00 €
Conector BLK 1x2 | 1729128 | https://www.digikey.com/en/products/detail/phoenix-contact/1729128/260615 | 2 | 2000 | 0.84 € | 1684.40 € | Conector BLK 1x2 | 1729128 | https://www.digikey.com/en/products/detail/phoenix-contact/1729128/260615 | 2 | 40000 | 0.84 € | 33688.00 €
Conector BLK 1x3 | 1729131 | https://www.digikey.com/en/products/detail/phoenix-contact/1729131/260616 | 2 | 2000 | 1.27 € | 2542.00 € | Conector BLK 1x3 | 1729131 | https://www.digikey.com/en/products/detail/phoenix-contact/1729131/260616 | 2 | 40000 | 1.27 € | 50840.00 €
Relé | RT314012 | https://www.mouser.es/ProductDetail/TE-Connectivity-PB/RT314012?qs=h4sDRd%2FXttjfRhAgOQMm4w%3D%3D | 2 | 2000 | 2.32 € | 4640.00 € | Relé | RT314012 | https://www.mouser.es/ProductDetail/TE-Connectivity-PB/RT314012?qs=h4sDRd%2FXttjfRhAgOQMm4w%3D%3D | 2 | 40000 | 2.28 € | 91200.00 €
Transistor BJT | 2N2222 | https://www.digikey.es/es/products/detail/central-semiconductor-corp/2N2222-PBFREE/4806844?gQT=2 | 2 | 2000 | 0.92 € | 1846.00 € | Transistor BJT | 2N2222 | https://www.digikey.es/es/products/detail/central-semiconductor-corp/2N2222-PBFREE/4806844?gQT=2 | 2 | 40000 | 0.91 € | 36520.00 €
Botón | PTS526SK15SMTR2-LFS | https://www.digikey.es/es/products/detail/c-k/PTS526SK15SMTR2-LFS/10056626 | 4 | 4000 | 0.08 € | 323.60 € | Botón | PTS526SK15SMTR2-LFS | https://www.digikey.es/es/products/detail/c-k/PTS526SK15SMTR2-LFS/10056626 | 4 | 80000 | 0.07 € | 5592.80 €
Microcontrolador | PIC18F2580-I/SO | https://www.mouser.es/ProductDetail/Microchip-Technology/PIC18F2580-I-SO?qs=5Wx0vN22rFLg5k%2FqM4Xm9A%3D%3D | 1 | 1000 | 7.72 € | 7720.00 € | Microcontrolador | PIC18F2580-I/SO | https://www.mouser.es/ProductDetail/Microchip-Technology/PIC18F2580-I-SO?qs=5Wx0vN22rFLg5k%2FqM4Xm9A%3D%3D | 1 | 20000 | 7.72 € | 154400.00 €
Sensor de lluvia | HDC2010YPAR | https://www.mouser.es/ProductDetail/Texas-Instruments/HDC2010YPAR?qs=EU6FO9ffTwc2CasHMLP4bA%3D%3D | 1 | 1000 | 0.99 € | 988.00 € | Sensor de lluvia | HDC2010YPAR | https://www.mouser.es/ProductDetail/Texas-Instruments/HDC2010YPAR?qs=EU6FO9ffTwc2CasHMLP4bA%3D%3D | 1 | 20000 | 0.90 € | 18060.00 €
Amplificador Operacional | LT1716 | https://www.mouser.es/ProductDetail/Analog-Devices/LT1716IS5TRMPBF?qs=ytflclh7QUVIaNMG%252B3EIxQ%3D%3D | 2 | 2000 | 2.06 € | 4120.00 € | Amplificador Operacional | LT1716 | https://www.mouser.es/ProductDetail/Analog-Devices/LT1716IS5TRMPBF?qs=ytflclh7QUVIaNMG%252B3EIxQ%3D%3D | 2 | 40000 | 2.05 € | 82000.00 €
Transceptor de Voltaje | TXS0108EPWR | https://www.mouser.es/ProductDetail/Texas-Instruments/TXS0108EPWR?qs=IUbkBnfnSQLgiWtCbWtYOw%3D%3D | 1 | 1000 | 0.58 € | 581.00 € | Transceptor de Voltaje | TXS0108EPWR | https://www.mouser.es/ProductDetail/Texas-Instruments/TXS0108EPWR?qs=IUbkBnfnSQLgiWtCbWtYOw%3D%3D | 1 | 20000 | 0.54 € | 10820.00 €
Puente H | DRV8871DDA | https://www.digikey.com/es/products/detail/texas-instruments/DRV8871DDA/6110574 | 2 | 2000 | 1.76 € | 3520.00 € | Puente H | DRV8871DDA | https://www.digikey.com/es/products/detail/texas-instruments/DRV8871DDA/6110574 | 2 | 40000 | 1.76 € | 70400.00 €
Controlador CAN | MCP2551 | https://www.mouser.es/ProductDetail/Microchip-Technology/MCP2551-E-SN?qs=Vn0zuzr35GHkGDCgnw0F9A%3D%3D | 1 | 1000 | 1.26 € | 1260.00 € | Controlador CAN | MCP2551 | https://www.mouser.es/ProductDetail/Microchip-Technology/MCP2551-E-SN?qs=Vn0zuzr35GHkGDCgnw0F9A%3D%3D | 1 | 20000 | 1.26 € | 25200.00 €
Conector DB9 | SD9S | https://www.digikey.es/es/products/detail/l-com/SD9S/21288632 | 2 | 2000 | 2.50 € | 5000.00 € | Conector DB9 | SD9S | https://www.digikey.es/es/products/detail/l-com/SD9S/21288632 | 2 | 40000 | 2.35 € | 93920.00 €
Cristal | HC-49/U | https://www.digikey.es/es/products/detail/citizen-finedevice-co-ltd/HC-49-U-S16384000ABJB/284225 | 1 | 1000 | 0.32 € | 323.00 € | Cristal | HC-49/U | https://www.digikey.es/es/products/detail/citizen-finedevice-co-ltd/HC-49-U-S16384000ABJB/284225 | 1 | 20000 | 0.28 € | 5618.00 €
PCB | - | https://cart.jlcpcb.com/quote?orderType=1&stencilLayer=1&stencilWidth=100&stencilLength=100&stencilCounts=2000 | 1 | 1000 | 0.41 € | 405.60 € | PCB | - | https://cart.jlcpcb.com/quote?orderType=1&stencilLayer=1&stencilWidth=100&stencilLength=100&stencilCounts=2000 | 1 | 20000 | 0.32 € | 6313.00 €
 |  |  |  |  | Total: | 39733.20 € |  |  |  |  |  | Total: | 768725.00 €
 |  |  |  |  | Total por placa: | 39.73 € |  |  |  |  |  | Total por placa: | 38.44 €

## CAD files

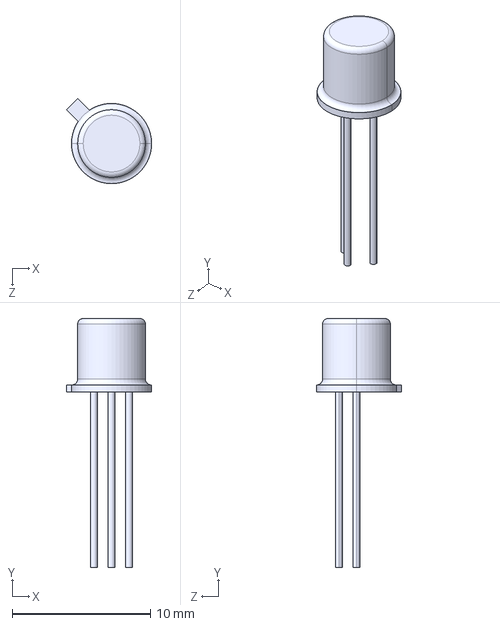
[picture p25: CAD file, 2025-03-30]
Proyecto_ArgibayManuel_YangAlex/Externos/2N2222/2N2222.step
6.17 x 18.0 x 6.17 mm

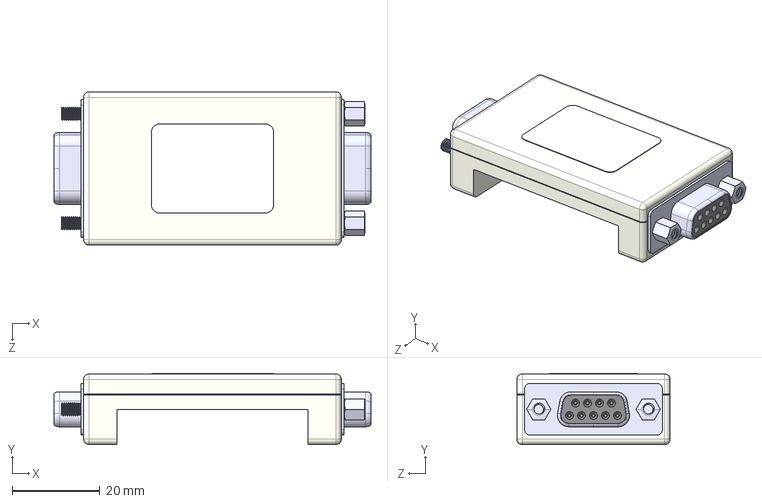
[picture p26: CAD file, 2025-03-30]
Proyecto_ArgibayManuel_YangAlex/Externos/DB9/DB9.step
72.4 x 16.3 x 35.1 mm

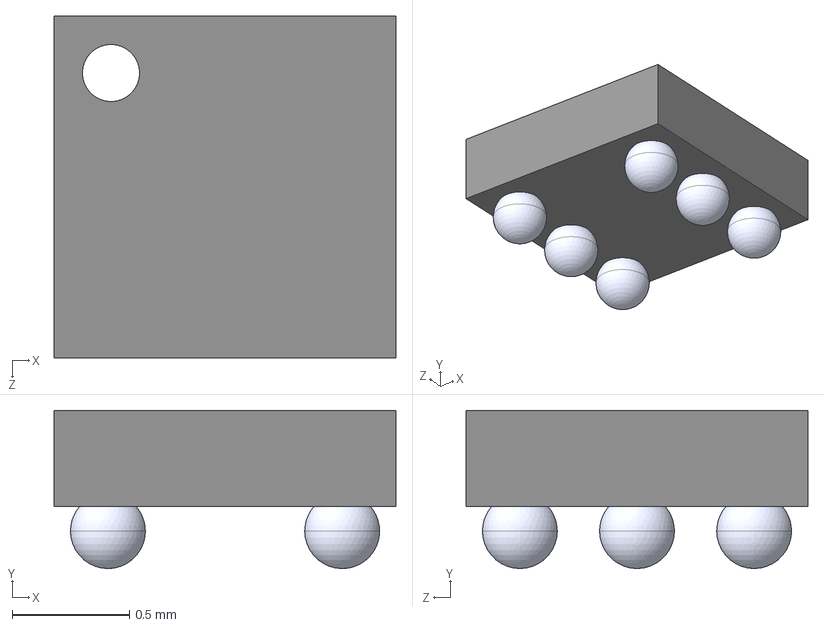
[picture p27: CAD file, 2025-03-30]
Proyecto_ArgibayManuel_YangAlex/Externos/HDC2010YPAR/HDC2010YPAR.step
1.46 x 0.675 x 1.46 mm

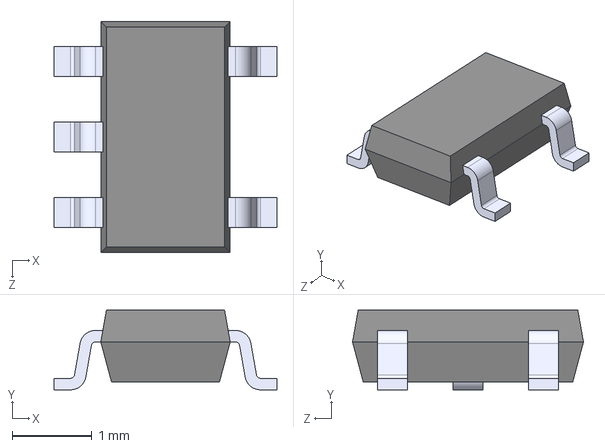
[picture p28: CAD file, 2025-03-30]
Proyecto_ArgibayManuel_YangAlex/Externos/LT1716IS5TRMPBF/LT1716IS5TRMPBF.step
2.80 x 1.00 x 2.90 mm

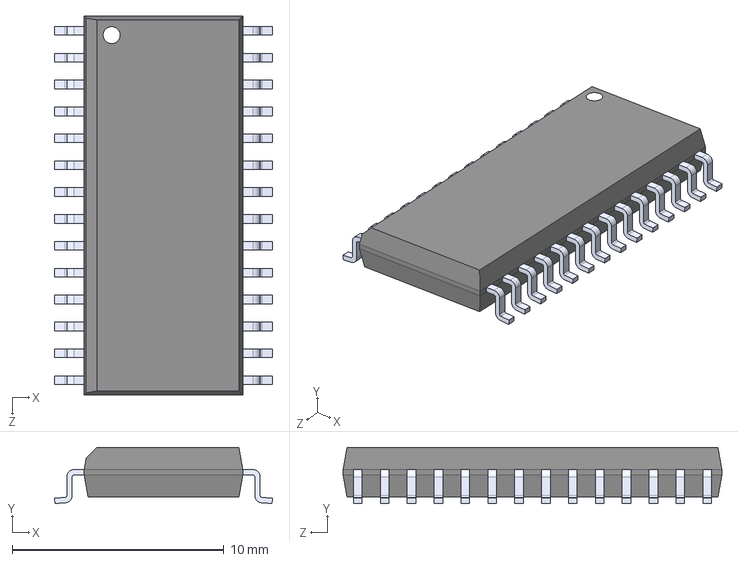
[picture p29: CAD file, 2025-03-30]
Proyecto_ArgibayManuel_YangAlex/Externos/PIC18F258-I_SO/PIC18F258-I_SO.step
10.3 x 2.65 x 17.9 mm

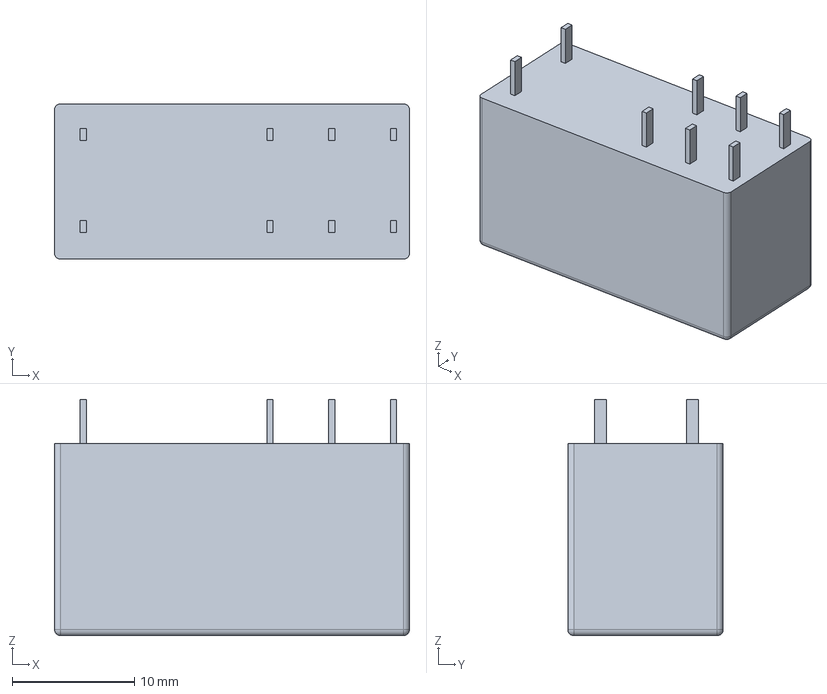
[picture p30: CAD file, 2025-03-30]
Proyecto_ArgibayManuel_YangAlex/Externos/RT314012/RT314012.step
29.0 x 12.7 x 19.3 mm

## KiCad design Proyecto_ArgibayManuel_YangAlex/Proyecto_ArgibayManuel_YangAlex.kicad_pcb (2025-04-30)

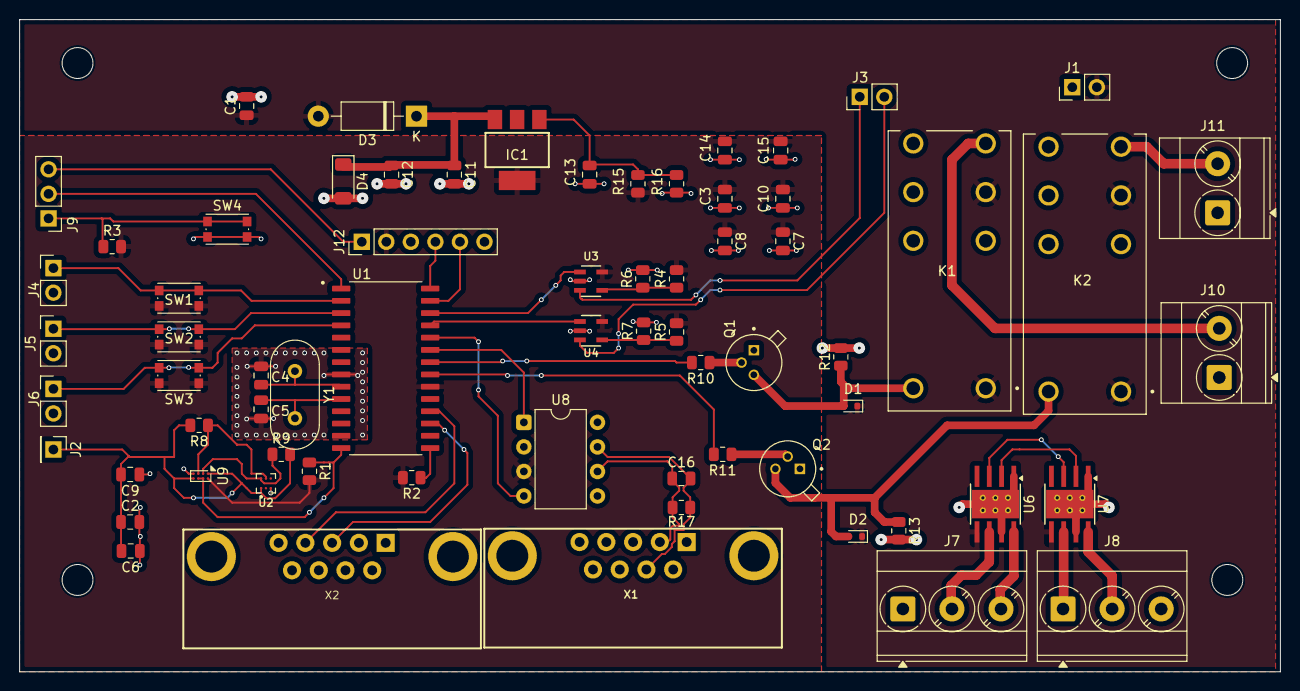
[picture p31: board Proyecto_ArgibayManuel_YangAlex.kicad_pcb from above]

Board: 2 copper layers, 130.5 x 67.5 mm, 68 parts (0 on the bottom side), 47 nets.

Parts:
C1, C2, C3, C6, C7, C8, C9, C10, C11, C13, C15: 100nF; C_0805_2012Metric
C4, C5: 33pF; C_0805_2012Metric
C12, C14: 1uF; C_0805_2012Metric
C16: 100pF; C_0805_2012Metric
D1, D2: 1N4148WT; D_SOD-523
D3: 1N4002; D_DO-41_SOD81_P10.16mm_Horizontal
D4: BZV55C6V2; D_MiniMELF
IC1: LM1117
J1: Conn_01x02; PinHeader_1x02_P2.54mm_Vertical
J2: Conn_01x01; PinHeader_1x01_P2.54mm_Vertical
J3, J4, J5, J6: Con_1x2; PinHeader_1x02_P2.54mm_Vertical
J7, J8: Conn_01x03; TerminalBlock_Phoenix_MKDS-3-3-5.08_1x03_P5.08mm_Horizontal
J9: Conn_01x03_Pin; PinHeader_1x03_P2.54mm_Vertical
J10, J11: Con_1x2; TerminalBlock_Phoenix_MKDS-3-2-5.08_1x02_P5.08mm_Horizontal
J12: Con_ICSP; PinHeader_1x06_P2.54mm_Vertical
K1, K2: RT314012
Q1, Q2: 2N2222
R1, R2, R8, R9: 4.7K; R_0805_2012Metric
R3: 300; R_0805_2012Metric
R4, R5: 3k; R_0805_2012Metric
R6, R7: 2k; R_0805_2012Metric
R10, R11, R12, R13, R15, R16: 1k; R_0805_2012Metric
R17: 60; R_0805_2012Metric
SW1, SW2, SW3, SW4: SW_Push; SW_Push_1P1T_NO_CK_KMR2
U1: PIC18F258-I_SO; PIC18F258
U2: HDC2010YPAR
U3, U4: LT1716IS5TRMPBF; LT1716
U6, U7: DRV8871DDA; Texas_HTSOP-8-1EP_3.9x4.9mm_P1.27mm_EP2.95x4.9mm_Mask2.4x3.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
U8: MCP2551-I-P; DIP-8_W7.62mm
U9: SN74LVC2T45YZP; Texas_DSBGA-8_0.9x1.9mm_Layout2x4_P0.5mm
X1, X2: DB9
Y1: Crystal; Crystal_HC49-U_Vertical

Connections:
+3.3V: C2.1, C6.2, C9.2, J2.1, R8.2, R9.2, U2.A1 (VDD), U9.A1 (VCCA), U9.D2 (DIR)
Bomba: J10.2, K1.14-1
CAN+: C16.2, R17.2, U8.7 (CANH), X1.7
CAN-: C16.1, R17.1, U8.6 (CANL), X1.2
C_R_Bombas_agua: R10.2, U1.22 (RB1/INT1)
C_R_Calefactor: R11.2, U1.21 (RB0/INT0)
Calefactor: J11.2, K2.14-1
F_C_In1: J3.2, U4.3 (+IN)
F_C_In2: J3.1, U3.3 (+IN)
F_C_Out1: U1.25 (RB4), U4.1 (OUT)
F_C_Out2: U1.26 (RB5/PGM), U3.1 (OUT)
GND: C2.2, C3.2, C4.2, C5.2, C6.1, C7.2, C8.2, C9.1, C10.2, C13.2, C14.2, C15.2, J4.2, J5.2, J6.2, J12.3 (VSS), J12.6 (PGM/LVP), R6.2, R7.2, R16.1, SW4.2, U1.8 (VSS), U2.C1 (GND), U3.2 (V-), U4.2 (V-), U8.2 (VSS), U8.8 (Rs), U9.D1 (GND), X1.9, X2.2
GNDPWR: C1.2, C11.2, C12.2, D4.2 (A), J1.1, J7.1, J8.3, J10.1, J11.1, Q1.1, Q2.1, R12.2, R13.2, U6.1 (GND), U6.7 (GND), U6.9 (GND), U7.1 (GND), U7.7 (GND), U7.9 (GND)
Int_Bomba_de_Agua: J6.1, SW3.2, U1.4 (RA2/AN2/VREF-)
Int_Calefactor: J5.1, SW2.2, U1.3 (RA1/AN1)
Int_limpiaparabrisas: J4.1, SW1.2, U1.2 (RA0/AN0/CVREF)
MCLR: J9.2, U1.1 (~MCLR/VPP)
Motor_Izquierdo_1: J7.3, U6.8 (OUT2)
Motor_derecho_1: J8.2, U7.8 (OUT2)
Motor_derecho_2: J8.1, U7.6 (OUT1)
Motor_izquierdo_2: J7.2, U6.6 (OUT1)
unnamed: C13.1, IC1.1, R15.1, R16.2
unnamed: D1.2 (A), K1.A2, Q1.3, R12.1
unnamed: D2.2 (A), K2.A2, Q2.3, R13.1
unnamed: C11.1, C12.1, D3.1 (K), D4.1 (K), IC1.3
unnamed: J9.1, R3.1, SW4.1
unnamed: Q1.2, R10.1
unnamed: Q2.2, R11.1
unnamed: R4.1, R6.1, U3.4 (-IN)
unnamed: R5.1, R7.1, U4.4 (-IN)
PGC: J12.5 (PGC/ICSPCLK), U1.27 (RB6/PGC)
PGD: J12.4 (PGD/ICSPDAT), U1.28 (RB7/PGD)
PH_M_in1: U6.3 (IN1), U7.3 (IN1)
PH_M_in2: U6.2 (IN2), U7.2 (IN2)
RC6: U1.17 (RC6/TX/CK), X2.3
RC7: U1.18 (RC7/RX/DT), X2.4
RX: U1.24 (RB3/CANRX), U8.4 (RXD)
SCL_3,3V: R8.1, U2.B2 (SCL), U9.C1 (A2)
SCL_5V: R1.1, U1.14 (RC3/SCK/SCL), U9.B2 (B1), U9.C2 (B2)
SDA_3,3V: R9.1, U2.A2 (SDA), U9.B1 (A1)
SDA_5V: R2.1, U1.15 (RC4/SDI/SDA)
TX: U1.23 (RB2/CANTX/INT2), U8.1 (TXD)
TX1: C4.1, U1.9 (OSC1/CLKI), Y1.1
TX2: C5.1, U1.10 (OSC2/CLKO/RA6), Y1.2
VBat: C1.1, D1.1 (K), D2.1 (K), D3.2 (A), J1.2, K1.11-1, K1.A1, K2.11-1, K2.A1, U6.5 (VM), U7.5 (VM)
VCC: C3.1, C7.1, C8.1, C10.1, C14.1, C15.1, IC1.4, J12.2 (VDD), R1.2, R2.2, R3.2, R4.2, R5.2, R15.2, SW1.1, SW2.1, SW3.1, U1.20 (VDD), U3.5 (V+), U4.5 (V+), U8.3 (VDD), U9.A2 (VCCB)
VPP: J9.3, J12.1 (~MCLR/VPP)

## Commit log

2025-03-25 Cambio título del proyecto
    [Proyecto_ArgibayManuel_YangAlex.kicad_sch]
2025-03-26 Modificación de esquemático y presentación de pptx
    [Proyecto_ArgibayManuel_YangAlex.kicad_sch]
2025-03-26 Agrego net classes, proyecto y cambio de presentación
    [Proyecto_ArgibayManuel_YangAlex.kicad_pcb, Proyecto_ArgibayManuel_YangAlex.kicad_sch]
2025-03-26 Modifique,netlist,Final de Carrera,GNDPWR,,seperar botonera
    Cambios
    [Proyecto_ArgibayManuel_YangAlex.kicad_sch]
2025-03-26 Separacion del circuito
    [Proyecto_ArgibayManuel_YangAlex.kicad_sch, untitled.kicad_sch]
2025-03-29 Modifico simulaciones del comparador y arreglo esquemático
    [Motores.kicad_sch, Proyecto_ArgibayManuel_YangAlex.kicad_sch]
2025-03-30 Ordenar esquematico
    [Buses.kicad_sch, Microlador(componentes).kicad_sch, Motores.kicad_sch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]
2025-03-30 arreglar errores con los esquematicos
    [Microlador(componentes).kicad_sch, Regulador de tension.kicad_sch, untitled.kicad_sch]
2025-03-30 empezando a añadir el sensor(aun no esta terminado)
    [Proyecto_ArgibayManuel_YangAlex.kicad_sch]
2025-03-31 Arreglo net classes, agrego DB-9
    [Buses.kicad_sch, Motores.kicad_sch, Proyecto_ArgibayManuel_YangAlex.kicad_sch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]
2025-03-31 Modifico los footprints
    [2N2222.step, DB9.step, HDC2010YPAR.step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]
2025-03-31 Empiezo layout, cambio footprints y arreglo esquematico
    [Buses.kicad_sch, Motores.kicad_sch, Proyecto_ArgibayManuel_YangAlex.kicad_pcb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]
2025-03-31 Conexiones(no acabado)
    [Proyecto_ArgibayManuel_YangAlex.kicad_pcb]
2025-03-31 Cambio layout (faltan agregar vías y reorganizar con la capa BOTTOM)
    [Motores.kicad_sch, Proyecto_ArgibayManuel_YangAlex.kicad_pcb, Proyecto_ArgibayManuel_YangAlex.kicad_sch]
2025-04-01 Termino layout (faltan acomodar etiquetas en la pcb))
    [Proyecto_ArgibayManuel_YangAlex.kicad_pcb, Proyecto_ArgibayManuel_YangAlex.kicad_sch]
2025-04-01 Arreglo nodos no conectados
    [Proyecto_ArgibayManuel_YangAlex.kicad_pcb]
2025-04-01 cambio del crystal
    [Proyecto_ArgibayManuel_YangAlex.kicad_pcb]
2025-04-01 Cambio de presentacion(esquematico,consumo,layout), minimas correciones en el esquematico
    [Buses.kicad_sch, Motores.kicad_sch, Proyecto_ArgibayManuel_YangAlex.kicad_sch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]
2025-04-01 nombrar etiqueta pcb
    [Proyecto_ArgibayManuel_YangAlex.kicad_pcb]
2025-04-01 Ligero cambio en la presentacion
2025-04-02 Arreglo errores y cambio conector
    [Proyecto_ArgibayManuel_YangAlex.kicad_pcb, Regulador de tension.kicad_sch]
2025-04-02 Arreglo errores del DRC. falta arreglar errores del GNDPWR
    [Proyecto_ArgibayManuel_YangAlex.kicad_pcb]
2025-04-02 Preentrega final
    [Proyecto_ArgibayManuel_YangAlex.kicad_pcb]
2025-04-02 Agrego cambios
    [Buses.kicad_sch, Proyecto_ArgibayManuel_YangAlex.kicad_pcb, Proyecto_ArgibayManuel_YangAlex.kicad_sch]
2025-04-07 Arreglo layout y esqumatico con las correcciones pasadas
    [Motores.kicad_sch, Proyecto_ArgibayManuel_YangAlex.kicad_pcb, Proyecto_ArgibayManuel_YangAlex.kicad_sch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]
2025-04-07 Separacion de Botonera
    [Buses.kicad_sch, Motores.kicad_sch, Proyecto_ArgibayManuel_YangAlex.kicad_sch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]
2025-04-07 cambio de valores de los Condensadores del oscilador
    [Proyecto_ArgibayManuel_YangAlex.kicad_sch]
2025-04-07 cambio de diagrama de bloques
2025-04-08 Reglas de disenyo(requeriments)
2025-04-08 cambiar esquematico
    [Buses.kicad_sch, Motores.kicad_sch, Proyecto_ArgibayManuel_YangAlex.kicad_pcb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]
2025-04-08 Cambio de la PCB(por el cambio de elos conectores)
    [Proyecto_ArgibayManuel_YangAlex.kicad_pcb, Proyecto_ArgibayManuel_YangAlex.kicad_sch]
2025-04-09 Cambio del sensor
    [Buses.kicad_sch, Motores.kicad_sch, Proyecto_ArgibayManuel_YangAlex.kicad_pcb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]
2025-04-23 Arreglo layout y esquematico (DRC correcto)
    [Proyecto_ArgibayManuel_YangAlex.kicad_pcb, Proyecto_ArgibayManuel_YangAlex.kicad_sch]
2025-04-23 Empiezo presupuesto
    [Presupuesto.xlsx, Proyecto_ArgibayManuel_YangAlex BOM.csv]
2025-04-23 Cambio de Traductor bidireccional
    [Proyecto_ArgibayManuel_YangAlex.kicad_pcb, Proyecto_ArgibayManuel_YangAlex.kicad_sch]
2025-04-23 Presupuesto final y gerbers del layout
    [Presupuesto.xlsx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]
2025-04-23 traductor bidireccional(layout)
    [Proyecto_ArgibayManuel_YangAlex.kicad_pcb]
2025-04-23 Cambiamos traductor bidireccional
    [Proyecto_ArgibayManuel_YangAlex-BOTTOM.gbr, Proyecto_ArgibayManuel_YangAlex-B_Mask.gbr, Proyecto_ArgibayManuel_YangAlex-B_Paste.gbr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]
2025-04-23 Cambios en la presentacion

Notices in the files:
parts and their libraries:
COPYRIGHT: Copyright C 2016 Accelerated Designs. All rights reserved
